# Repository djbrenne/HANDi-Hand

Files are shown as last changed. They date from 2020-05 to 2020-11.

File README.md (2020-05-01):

# HANDi-Hand
Personal, unt-tested, un-released versions of HANDi Hand files. For verified and supported versions, see github.com/blincdev.

**MUX_Assembly.STEP:** The current version of the wrist MUX prototype, including connectors for sensors, servos, and out-of-wrist wires.

**Fit Test.STEP:** An assembly with all the relevant components for testing the fit of the MUX board in the wrist.

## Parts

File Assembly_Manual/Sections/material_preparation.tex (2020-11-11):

% Material Preparation

\chapter{Material Preparation}  % Main chapter title

\label {Material Preparation} 
%---------------------------------------------------------------------------------------------------------------------------------------
%
% MATERIAL PREPARATION
%
%---------------------------------------------------------------------------------------------------------------------------------------

\section{3D Printed Parts}
\textit{Estimated time 17h 0m}

\section{Potentiometers}
\textit{Estimated time 1h 45m}

In the current version, there are nine potentiometers (limited due to the number of analog input pins on the Arduino Mega). The suggested lengths of the connecting wires are found in Table \ref{potentiometer_table}.

\begin{table}[H]
\centering
\caption{Suggested wire lengths for potentiometers}
\label{potentiometer_table}
\begin{tabular}{| l | l |}
\hline
\textbf{Potentiometer ID} & \textbf{Suggested Wire Length}  \\ \hline
D0 & 150 mm \\ \hline
D1P & 150 mm \\ \hline
D1D & 190 mm \\ \hline
D2P & 150 mm \\ \hline
D2I & 190 mm \\ \hline
D3P & 150 mm \\ \hline
D3I & 190 mm \\ \hline
D4P & 150 mm \\ \hline
D5P & 150 mm \\ \hline
\end{tabular}
\end{table} 

Figure \ref{pot_pins} describes the polarity of the potentiometers. To prepare the potentiomters:

\begin{enumerate}
\item Cut off the top lone pin on the potentiometer as short as possible.
\item Solder the wires to the potentiometer and a straight pin header to the other end of each wire. See note below about D0.
\item Use black heat-shrink on the connections near the potentiometer, and coloured heat shrink on the far connections corresponding to the polarity noted in Figure 7.
\item Heat shrink the 3 wires together near the loose end using a light coloured heat shrink tubing. Label the wires here with the potentiometer ID.
\end{enumerate}
\textbf{Note:}  the straight pin headers for the D0 potentiometer must be soldered to the wires \textit{after} the potentiometer is installed in MC – Geared Rotator, and the wires routed through the narrow channel. Black heat-shrink tubing near the potentiometer will not fit in this channel, so it is omitted. 
\begin{figure}[H]
\centering
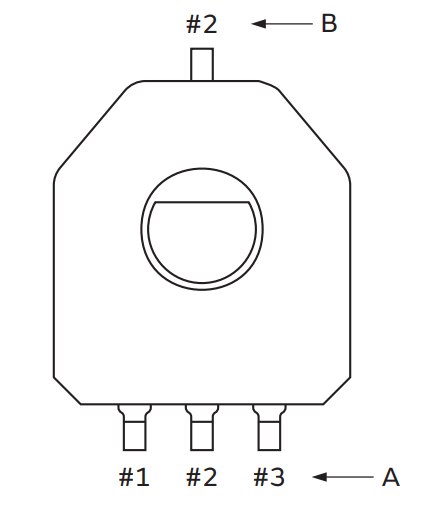
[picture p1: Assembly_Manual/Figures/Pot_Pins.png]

\caption{Potentiometer terminals diagram, viewed from the top (black side facing you). Pin \#1 is GND, pins labelled \#2 are SIG, and pin \#3 is VCC.}
\label{pot_pins}
\end{figure}

\section{FSRs}
\textit{Estimated time 1h 0m}

Each fingertip requires an FSR. The recommended wire length for finger FSRs is 250 mm; for the thumb FSR 200 mm is recommended. 
\begin{enumerate}
\item Solder each wire to the solder tabs of the FSR. 
\item Install FSR in fingertip (see 5.3.1 ).
\item Use black heat-shrink tubing on the connections near the FSR.
\item Solder the wires to straight pin headers.
\item Use yellow and red heat shrink tubing on the connections with the straight pin headers.
\item Heat shrink the two wires together using a light coloured heat shrink, and label the wires here with the ID of the finger they represent.
\end{enumerate}

\section{Screws}

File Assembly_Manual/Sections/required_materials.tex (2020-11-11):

% Required Materials

\chapter{Required Materials}  % Main chapter title

\label {Required Materials} % For referencing the chapter elsewhere, use \ref{Required Materials} 

%----------------------------------------------------------------------------------------

% Define some commands to keep the formatting separated from the content 
\newcommand{\keyword}[1]{\textbf{#1}}
\newcommand{\tabhead}[1]{\textbf{#1}}
\newcommand{\code}[1]{\texttt{#1}}
\newcommand{\file}[1]{\texttt{\bfseries#1}}
\newcommand{\option}[1]{\texttt{\itshape#1}}

%----------------------------------------------------------------------------------------

\section{3D Printed Parts}

The 3D printed parts are designed to be printed in PLA without support material and without rafts, except where indicated. Parts are designed for the print tolerance of a MakerBot Replicator 2. Some filing may be necessary to ensure a smooth running fit between parts.

All files required for 3D printing can be accessed via \href{https://blincdev.ca/}{BLINCdev.ca}. The suggested print specifications for each part are found in Table \ref{3d_printed_parts_list}. The table lists all of the part sets that must be printed for a complete hand. In the event that a particular component is needed, the individual STL files can be found on  \href{https://blincdev.ca/}{BLINCdev.ca} in addition to the grouped parts in Table \ref{3d_printed_parts_list}.

\begin{table}[H]
\centering
\caption{3D Printed Parts Specifications}
\label{3d_printed_parts_list}
\begin{tabular}{|p{4cm}|p{4cm}|p{2cm}|p{2.5cm}|}
\hline
\textbf{Part Name} & \textbf{Print Specifications} & \textbf{Estimated Print Time} & \textbf{Est. Material Weight} \\ \hline
Dorsal Palm & 0.2mm layer, 30\% infill, print with raft & 6h 0m & 64 g \\ \hline
Ventral Palm & 0.2 mm layer, 10\% infill & 1h 55m & 22 g  \\ \hline
Thumb Screw Cap &0.2 mm layer, 10\% infill &0h 15m &2 g  \\ \hline
D2 Full Finger &0.1 mm layer, 50\% infill &3h 36m &11 g  \\ \hline
D3 Full Finger &0.1 mm layer, 50\% infill &3h 36m &11 g  \\ \hline
D4 Full Finger &0.1 mm layer, 50\% infill &3h 36m &11 g  \\ \hline
D5 Full Finger &0.1 mm layer, 50\% infill &3h 36m &11 g  \\ \hline
Full Thumb &0.2 mm layer, 10\% infill &2h 30m &25 g  \\ \hline
Breadboard &0.1 mm layer, 10\% infill &0h 25m &3 g  \\ \hline
Connector Hub &0.2 mm layer, 10\% infill &0h 15m &3 g  \\ \hline
Pot Activator Set of 15 &0.1 mm layer, 10\% infill &0h 10m &1 g  \\ \hline
Pot Placeholder Set of 6 &0.2 mm layer, 10\% infill &0h 10m &2 g  \\ \hline
Servo Spool Full Set &0.1 mm layer, 10\% infill &0h 25m &4 g  \\ \hline
Servo Spur Gear &0.1 mm layer, 10\% infill &0h 5m &1 g  \\ \hline
\textbf{TOTAL:}&\centering{-}  & \textit{\textbf{TODO}} & \textit{\textbf{TODO}} \\ \hline
\end{tabular}
\end{table} 

\section{Off-The-Shelf Parts}
The table below contains all the off-the-shelf parts required for building a complete HANDi Hand. Additional ordering information is provided in Appendix \ref{AppendixA}.
\begin{table}[H]
\centering
\caption{Off-the-Shelf Parts Specifications.\label{ots_parts_table}}
\begin{tabular}{| p{6cm}|  p{7cm} |  p{2cm} |}
\hline
 \textbf{Item} & \textbf{Part Number} & \textbf{QTY}\\ \hline
Rotary position sensor & MuRata SV03A103AEA01R00 & 9 \\ \hline
Force sensitive resistor & Interlink Electronics 34-00004 & 5 \\ \hline
Arduino Mega & Arduino A000067 & 1 \\ \hline
AC / DC 5V 2.5A wall adapter & Qualtek QAWA-18-5-US01 & 2 \\ \hline
DC barrel jack adapter (female) & Sparkfun PRT-10288 &  1 \\ \hline
10 k$\Omega$, 1/8W through-hole resistor & Stackpole Electronics CF18JT10K0 & 5 \\ \hline
12-position header pin (long) & Sullins Connector PREC012SACN-RC & 2 \\ \hline
12-position header pin (short) & Sullins Connector PREC012SAAN-RC & 6 \\ \hline
12-position female socket & Sullins Connector PPTC121LFBN-RC & 2 \\ \hline
3-position female socket & Sullins Connector PPPC031LFBN-RC & 14 \\ \hline
Heat shrink tubing, assorted & Sparkfun PRT-09353 & 1 \\ \hline
Analog RC servo motor & Dymond D47 & 6 \\ \hline
USB Webcam & Microsoft LifeCam HD-3000 & 1 \\ \hline
Textured Neoprene Rubber & McMaster-Carr 8445K61 & 1 \\ \hline
Continuous Flex Wire, 26 AWG & McMaster-Carr 7071K19 & 50 feet \\ \hline
M2 x 25 mm Cheese Head Slotted Machine Screw & McMaster-Carr 91800A023	& 23 \\ \hline
M2 18-8 Washer & McMaster-Carr 93475A195 & 16 \\ \hline
5.9" Zip-Tie & Qualtek 17-M150N-C & 9 \\ \hline
\end{tabular}
\end{table}

\section{Tools}
\begin {multicols}{2}
[
The following tools are required during assembly.]
\begin{itemize}
\item 3D printer
\item M2 screw cutter (or bolt cutters and large flat metal file)
\item Dremel tool with sanding wheel
\item 120 grit sandpaper
\item Small files
\item Narrow flat screwdriver
\item \#0 Philips screwdriver
\item Wire strippers / cutters
\item Soldering iron and solder
\item Heat gun
\item Hobby knife
\item Fine tweezers
\item Needlenose pliers
\end{itemize}
\end{multicols}

\section{Printed Circuit Board}
A custom in-wrist printed circuit board (PCB) has been designed to handle signal and power routing in and out of the hand. The EAGLE files for the PCB are available in the \href{https://github.com/BLINCdev/HANDi-Hand}{HANDi-Hand release repository.} Documentation regarding how to order a PCB from a board manufacturer using these files can also be found in the same location.

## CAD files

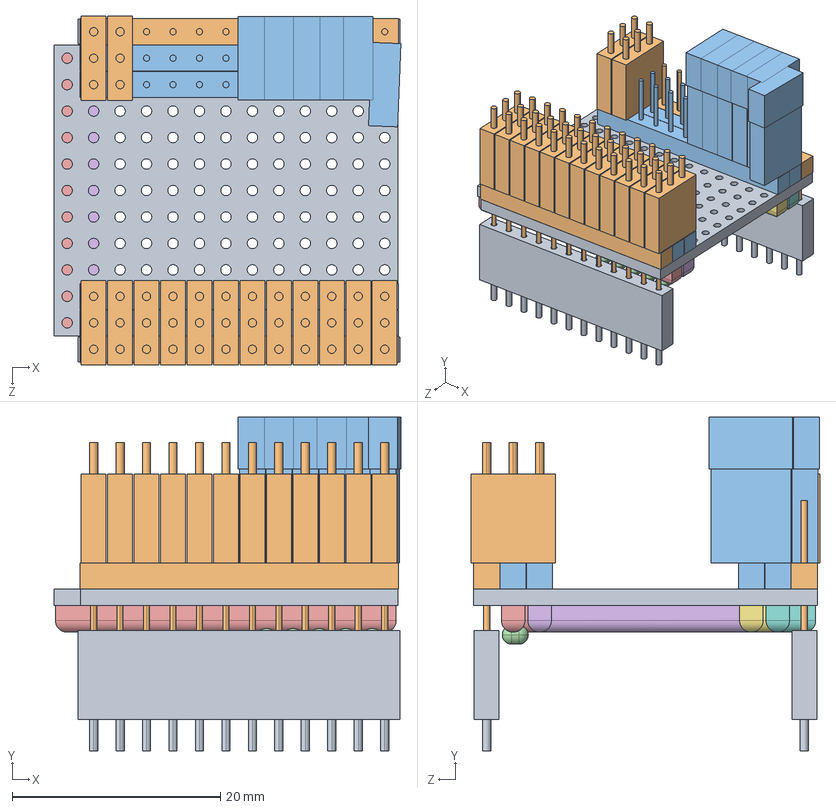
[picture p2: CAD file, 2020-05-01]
MUX_Assembly.STEP
33.3 x 32.0 x 33.5 mm
MUX-Mockup
Long_Conn_Header x 2
Short_Conn_Header x 4
10OHM_FSR x 5
Solder_Lines
Female_Conn_Header_12 x 2
Female_Conn_Header_3 x 14
Female_Conn_Header_Servo x 6

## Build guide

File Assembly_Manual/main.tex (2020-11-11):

%%%%%%%%%%%%%%%%%%%%%%%%%%%%%%%%%%%%%%%%%
% Dylan Brenneis - HANDi-Hand Assembly Manual
% 
% Drafted using the following template, modified for this manual:
%%%%%%%%%%%%%%%%%%%%%%%%%%%%%%%%%%%%%%%%%
% Masters/Doctoral Thesis 
% LaTeX Template
% Version 2.5 (27/8/17)
%
% This template was downloaded from:
% http://www.LaTeXTemplates.com
%
% Version 2.x major modifications by:
% Vel (vel@latextemplates.com)
%
% This template is based on a template by:
% Steve Gunn (http://users.ecs.soton.ac.uk/srg/softwaretools/document/templates/)
% Sunil Patel (http://www.sunilpatel.co.uk/thesis-template/)
%
% Template license:
% CC BY-NC-SA 3.0 (http://creativecommons.org/licenses/by-nc-sa/3.0/)
%
%%%%%%%%%%%%%%%%%%%%%%%%%%%%%%%%%%%%%%%%%

%----------------------------------------------------------------------------------------
%	PACKAGES AND OTHER DOCUMENT CONFIGURATIONS
%----------------------------------------------------------------------------------------

\documentclass[
11pt, % The default document font size, options: 10pt, 11pt, 12pt
oneside, % Two side (alternating margins) for binding by default, uncomment to switch to one side
english, % ngerman for German
% Single line spacing, alternatives: onehalfspacing or doublespacing
%draft, % Uncomment to enable draft mode (no pictures, no links, overfull hboxes indicated)
%nolistspacing, % If the document is onehalfspacing or doublespacing, uncomment this to set spacing in lists to single
%liststotoc, % Uncomment to add the list of figures/tables/etc to the table of contents
%toctotoc, % Uncomment to add the main table of contents to the table of contents
%parskip, % Uncomment to add space between paragraphs
%nohyperref, % Uncomment to not load the hyperref package
headsepline, % Uncomment to get a line under the header
chapterinoneline, % Uncomment to place the chapter title next to the number on one line
%consistentlayout, % Uncomment to change the layout of the declaration, abstract and acknowledgements pages to match the default layout
openany, % Comment out to have chapters, acknowledgements, etc. always start on a right-hand page (creates blank pages where necessary)
]{Manual} % The class file specifying the document structure

\usepackage[utf8]{inputenc} % Required for inputting international characters
\usepackage[T1]{fontenc} % Output font encoding for international characters
\usepackage{lipsum}
\usepackage{mathpazo} % Use the Palatino font by default
\usepackage{amsmath} % Math Package - db
\usepackage{pdfpages} % For picture quote page - db
\usepackage{siunitx}
\usepackage{float}
\usepackage[hidelinks]{hyperref}
\usepackage{caption}
\floatstyle{plaintop}
\restylefloat{table}
\usepackage{longtable}
\usepackage{multicol}
%\usepackage{lscape}
\usepackage{array}
\usepackage{ragged2e}
\newcolumntype{P}[1]{>{\RaggedRight\hspace{0pt}}p{#1}}
\usepackage{pdflscape}
%----------------------------------------------------------------------------------------
%	MARGIN SETTINGS
%----------------------------------------------------------------------------------------

\geometry{
	paper=letterpaper, % Change to letterpaper for US letter
	inner=2.5cm, % Inner margin
	outer=2.5cm, % Outer margin
	%bindingoffset=.5cm, % Binding offset
	top=2.5cm, % Top margin
	bottom=2.5cm, % Bottom margin
	head=21.986pt,
	%showframe, % Uncomment to show how the type block is set on the page
}

%----------------------------------------------------------------------------------------
%	MANUAL INFORMATION
%----------------------------------------------------------------------------------------

\manualtitle{HANDi-Hand Assembly Manual} % Your thesis title, this is used in the title and abstract, print it elsewhere with \ttitle
\author{Dylan J. A. \textsc{Brenneis}} % Your name, this is used in the title page and abstract, print it elsewhere with \authorname

\AtBeginDocument{
\hypersetup{pdftitle=\ttitle} % Set the PDF's title to your title
\hypersetup{pdfauthor=\authorname} % Set the PDF's author to your name
}

\begin{document}

\frontmatter % Use roman page numbering style (i, ii, iii, iv...) for the pre-content pages

\pagestyle{plain} % Default to the plain heading style until the thesis style is called for the body content

%----------------------------------------------------------------------------------------
%	TITLE PAGE
%----------------------------------------------------------------------------------------

\begin{titlepage}

\begin{figure}
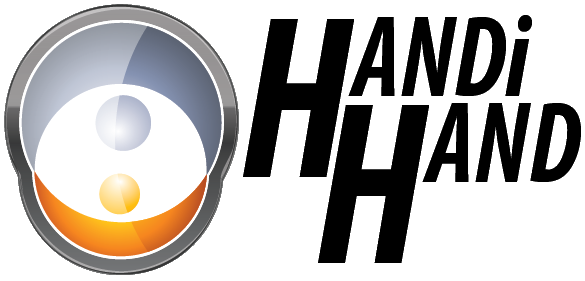
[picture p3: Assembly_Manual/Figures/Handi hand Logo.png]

\end{figure}

\begin{flushright}
\null
\vfill
{\Huge \bfseries \ttitle\par}\vspace{0.6cm} % Manual title
\Large{\textit{Version 2.0}}

\href{http://www.dylanbrenneis.ca}{Dylan J. A. Brenneis}\\%\authorname} % Author name - remove the \href bracket to remove the link
August 2020
\end{flushright}
\end{titlepage}

%----------------------------------------------------------------------------------------
%	INTRODUCTION PAGE
%----------------------------------------------------------------------------------------

\begin{abstract}
\setcounter{page}{2}
\addchaptertocentry{Introduction} % Add the abstract to the table of contents
The HANDi Hand is an open-source robotic platform specifically designed for machine learning research in prosthetic control. The inexpensive and easily modifiable hardware allows versatility for research studies, and the suite of sensors provides valuable information for machine learning and prosthetics research. 

This assembly manual outlines all the information required to print and source parts, and assemble the HANDi Hand as currently designed. The hand takes an estimated 30 hours to build.

The open-source release provides all solid-modelling files, .stl files, Arduino code, and assembly instruction required to construct a fully functional HANDi Hand, and should also give the maker enough flexibility to make alterations to the design as necessary to suit their own needs. Both left and right hand versions are available. To contact the original designers, or to receive support for your build, please visit  \href{https://blincdev.ca/}{BLINCdev.ca}.
\section*{Version 2.0 Updates}
The HANDi Hand was originally released in August 2017.\footnote{D. J. A. Brenneis, M. R. Dawson, P. M. Pilarski, “\href{https://sites.ualberta.ca/~pilarski/docs/papers/Brenneis_2017_MEC_preprint.pdf}{Development of the HANDi Hand: An Inexpensive, Multi-Articulating, Sensorized Hand for Machine Learning Research in Myoelectric Control},” Proc. of MEC’17: Myoelectric Controls Symposium, Fredericton, New Brunswick, August 15-18, 2017.} This updated assembly manual includes a number of changes that lower the overall cost and increase the ease of building the hand, as well as compensating for the discontinuation of the previous servo-motors. The hand's performance characteristics remain similar to that published in MEC '17. The main changes include:
\begin{itemize}
\item Redesign for Dymond D47 servos
\item Design of in-wrist PCB
\item Redesign for smaller, more inexpensive camera
\item Update specifications for UV-resistant zip-tie cables
\item More comprehensive build documentation, including assembly videos
\end{itemize}
\end{abstract}
%----------------------------------------------------------------------------------------
%	LIST OF CONTENTS/FIGURES/TABLES PAGES
%----------------------------------------------------------------------------------------

\tableofcontents % Prints the main table of contents

\listoftables % Prints the list of tables

\listoffigures % Prints the list of figures

%----------------------------------------------------------------------------------------
%	DEFINITIONS
%----------------------------------------------------------------------------------------
\newpage
\addchaptertocentry{Glossary of Terms}
\noindent\textbf{\Huge{Glossary of Terms}}
\vspace{1cm}

\noindent\textbf{Digits}: The digits are referred to by standard numbering, beginning with the thumb as D1 as shown in Figure~\ref{fig:finger_nums}.
\begin{figure}[H]
\centering
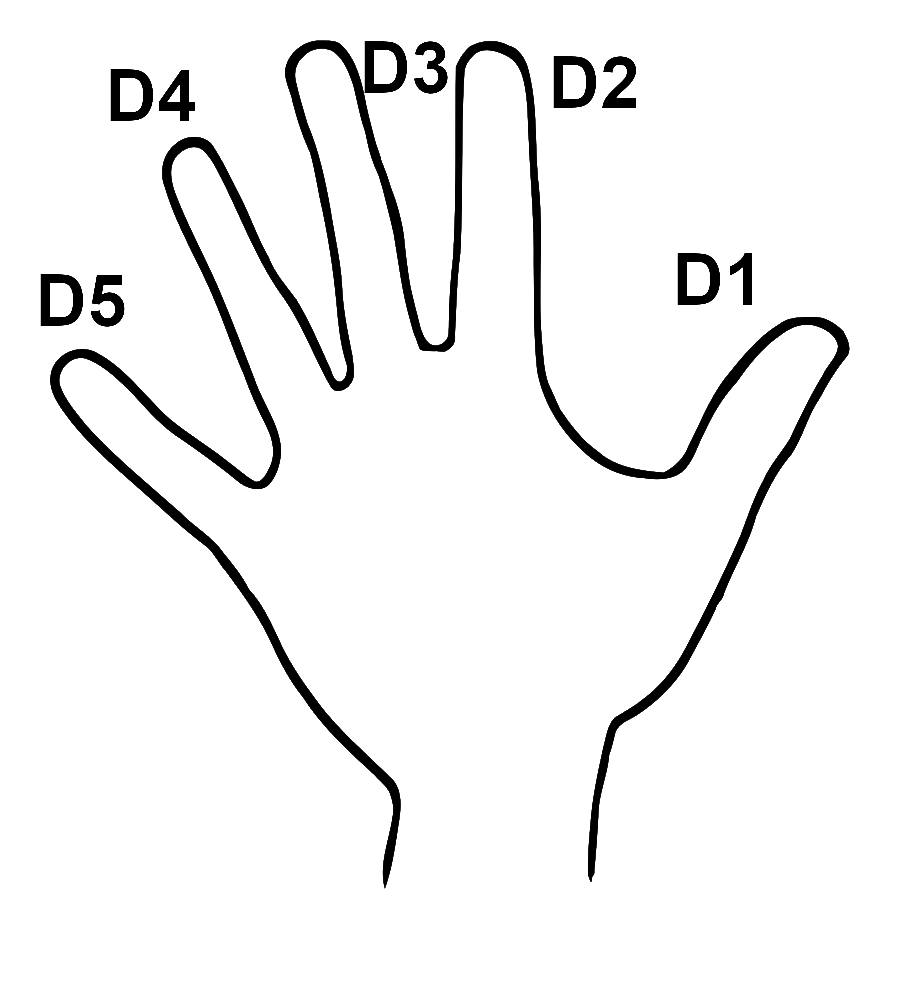
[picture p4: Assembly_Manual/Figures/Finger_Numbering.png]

\caption{Numbering scheme used for finger naming.}
\label{fig:finger_nums}
\end{figure}
\noindent\textbf{Joints}: The joints are named in accordance with Figure~\ref{fig:joint_nums}. The names are constructed first with a digit indicator (i.e. D2) followed by a joint indicator D, I or P, indicating distal, intermediate, or proximal respectively. Potentiometers are named for the joints that they measure. The digit D0 refers to thumb rotation.
\begin{figure}[H]
\centering
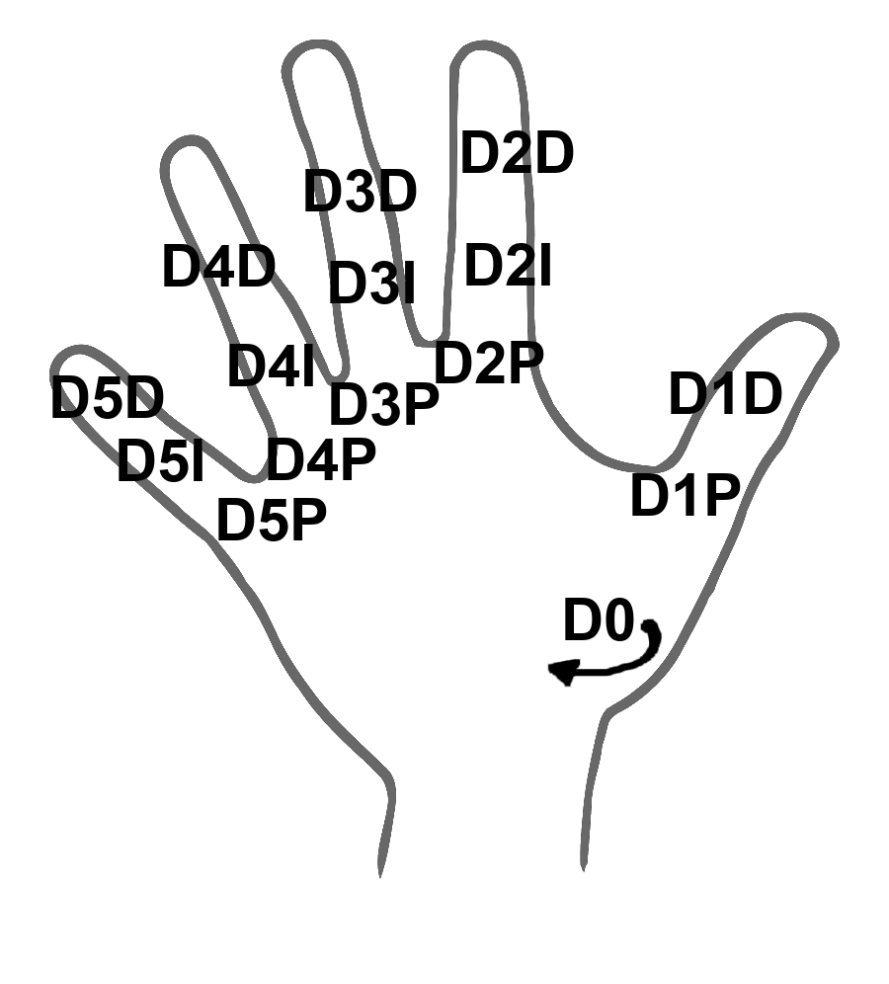
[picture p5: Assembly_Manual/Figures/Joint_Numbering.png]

\caption{Numbering scheme used for joint naming.}
\label{fig:joint_nums}
\end{figure}

\noindent\textbf{Finger Parts}: Each phalanx of the finger is made up of multiple parts. The part names are contrived according to the following convention:
\begin{enumerate}
\item Phalanx indicator. PP = Proximal Phalanx, IP = Intermediate Phalanx, DP = Distal Phalanx, MC = Metacarpal
\item Part position indicator. P = Proximal, D = Distal
\item Position modifier. There are sometimes multiple parts in the same location that must be differentiated by their function (pivot, main, lock, tip, etc).
\item Handedness indicator. R = Right Hand, L = Left Hand
\end{enumerate}
An example part name would be \textbf{IP-P Pivot R}, for the proximal portion of the intermediate phalanx corresponding to the pivot, for the right-hand version of the HANDi Hand.
\newpage

%----------------------------------------------------------------------------------------
%	MAIN CONTENT 
%----------------------------------------------------------------------------------------

\mainmatter % Begin numeric (1,2,3...) page numbering

\pagestyle{thesis} % Return the page headers back to the "thesis" style

% Include the steps of assembly as separate files from the Steps folder
% Uncomment the lines as you write the chapters

\include{Sections/required_materials}
\include{Sections/flowchart}
\include{Sections/material_preparation}
\include{Sections/thumb_assembly}
\include{Sections/finger_assembly}
\include{Sections/servo_installation}
\include{Sections/signal_board}
\include{Sections/ventral_palm}
\include{Sections/palm_grips}
\include{Sections/wiring}

%----------------------------------------------------------------------------------------
%	MANUAL CONTENT - APPENDICES
%----------------------------------------------------------------------------------------

\appendix % Cue to tell LaTeX that the following "chapters" are Appendices
% Include the appendices of the thesis as separate files from the Appendices folder
% Uncomment the lines as you write the Appendices

\include{Sections/appendix_a}
\include{Sections/appendix_b}
%\include{Appendices/AppendixC}

\end{document}

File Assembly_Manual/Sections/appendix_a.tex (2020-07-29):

% Appendix A

\chapter{Commercial Off-The-Shelf Parts Information} % Main appendix title

\label{AppendixA}

This appendix contains detailed ordering information for the off-the-shelf parts used in the HANDi Hand. Links to specific vendors are supplied for convenience only; no affiliation between BLINCdev and the vendors exists or is implied. Cost information is provided to give the builder an estimate of the cost of the project, and is accurate as of August 2020.
\newpage
%\begin{landscape}
\begin{longtable}{| P{3cm} | P{4cm} | P{2cm} | P{1cm} | P{1.5cm} | P{1.5cm} | P{1cm} |}
\caption{Detailed information for off-the-shelf parts used in the HANDi Hand. Click on part numbers for specific links.}
\label{detailed_cots}

\\ \hline \textbf{Item}  & \textbf{Part Number} & \textbf{Vendor} & \textbf{QTY} & \textbf{Cost / Item} & \textbf{Ext. Cost} & \textbf{Curr.} \\ \hline
\endfirsthead

\hline \textbf{Item}  & \textbf{Part Number} & \textbf{Vendor} & \textbf{QTY} & \textbf{Cost / Item} & \textbf{Ext. Cost} & \textbf{Curr.} \\ \hline
\endhead

\hline \multicolumn{7}{|r|}{\textit{Continued on next page...}} \\ \hline \endfoot

\hline \multicolumn{7}{|r|}{\textit{End of table.}} \\ \hline \endlastfoot

Rotary position sensor 						& \href{https://www.digikey.ca/en/products/detail/murata-electronics/SV03A103AEA01R00/4359898}{MuRata SV03A103AEA01R00} 														& DigiKey 			& 9 		& \$2.33 	& \$20.97		& CAD \\ \hline
Force sensitive resistor 						& \href{https://www.digikey.ca/en/products/detail/interlink-electronics/34-00004/2798665}{Interlink Electronics 34-00004}																& DigiKey 			& 5  		& \$16.20 	& \$71.08		& CAD \\ \hline
Arduino Mega 								& \href{https://www.digikey.ca/en/products/detail/arduino/A000067/2639006?s=N4IgTCBcDaIIwAYCsCC0i4A5UDkAiIAugL5A}{Arduino A000067} 												& DigiKey 			& 1 		& \$56.86 	& \$56.86		& CAD  \\ \hline
AC / DC 5V 2.5A wall adapter 					& \href{https://www.digikey.ca/en/products/detail/qualtek/QAWA-18-5-US01/6412294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}{Qualtek QAWA-18-5-US01}							& DigiKey 			& 2 		& \$25.33 	& \$50.66		& CAD \\ \hline
DC barrel jack adapter (female) 				& \href{https://www.digikey.ca/en/products/detail/sparkfun-electronics/PRT-10288/6163697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}{Sparkfun PRT-10288} 									& DigiKey	 		& 1 		& \$4.36 	& \$4.36		& CAD  \\ \hline
10 k$\Omega$, 1/8W through-hole resistor 		& \href{https://www.digikey.ca/en/products/detail/stackpole-electronics-inc/CF18JT10K0/1741566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}{Stackpole Electronics CF18JT10K0} 				& DigiKey 			& 5  		& \$0.16 	& \$0.80		& CAD \\ \hline
12-position header pin (long) 					& \href{https://www.digikey.ca/en/products/detail/sullins-connector-solutions/PREC012SACN-RC/2775974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}{Sullins Connector PREC012SACN-RC} 	& DigiKey 			& 2  		& \$0.49 	& \$0.98		& CAD \\ \hline
12-position header pin (short) 					& \href{https://www.digikey.ca/en/products/detail/sullins-connector-solutions/PREC012SAAN-RC/2774842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}{Sullins Connector PREC012SAAN-RC} 	& DigiKey 			& 6  		& \$0.38 	& \$2.28		& CAD \\ \hline
12-position female socket 						& \href{https://www.digikey.ca/en/products/detail/sullins-connector-solutions/PPTC121LFBN-RC/807231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}{Sullins Connector PPTC121LFBN-RC} 		& DigiKey 			& 2  		& \$1.15 	& \$2.30		& CAD \\ \hline
3-position female socket 						& \href{https://www.digikey.ca/en/products/detail/sullins-connector-solutions/PPPC031LFBN-RC/810175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}{Sullins Connector PPPC031LFBN-RC} 		& DigiKey 			& 14  	& \$0.55 	& \$7.25		& CAD \\ \hline
Heat shrink tubing, assorted 					& \href{https://www.digikey.ca/en/products/detail/qualtek/Q2-F-RK4-1-16-11-6IN-39/1210262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}{Qualtek Q2-F-RK4-1/16-11-6IN-39} 					& DigiKey	 		& 1 		& \$2.96 	& \$2.96		& CAD  \\ \hline
7.87" Black Zip-Tie 							& \href{https://www.digikey.ca/en/products/detail/advanced-cable-ties-inc/AL-08-18-0-C/10378818}{Advanced Cable Ties AL-08-18-0-C}														& DigiKey 			& Pack of 100\footnote{Only 5 zip-ties required for assembly.} 	& \$6.09 	& \$6.09		& CAD \\ \hline
Analog RC servo motor 						& \href{https://www.dymondusa.com/Servo-11305-D47-Power-Servo.html}{Dymond 11305 D47} 																					& Dymond 		& 6  		& \$21.95 	& \$131.70	& USD \\ \hline
USB Webcam 								& \href{https://www.amazon.ca/Microsoft-Lifecam-HD-3000-Webcam-Black/dp/B009VL9YJ2}{Microsoft LifeCam HD-3000} 																& Amazon 		& 1 		& \$38.59 	& \$38.59		& CAD  \\ \hline
1/32" Textured Neoprene Rubber, 40A Durometer 	& \href{https://www.mcmaster.com/8445K61-8445K161/}{McMaster-Carr 8445K61} 																							& McMaster-Carr 	& 12" x 12"		& \$12.45 & \$12.45		& USD \\ \hline
Continuous Flex Wire, 26 AWG 					& \href{https://www.mcmaster.com/7071K19/}{McMaster-Carr 7071K19} 																									& McMaster-Carr 	& 50 feet 			& \$1.20 	& \$60.00 		& USD  \\ \hline
M2 x 25 mm Cheese Head Slotted Machine Screw 	& \href{https://www.mcmaster.com/91800A023/}{McMaster-Carr 91800A023}																									& McMaster-Carr 	& Pack of 50*\footnote{Only 23 screws needed for assembly.}		& \$8.41 	& \$8.41		& USD  \\ \hline
M2 18-8 Washer 							& \href{https://www.mcmaster.com/93475A195/}{McMaster-Carr 93475A195}																									& McMaster-Carr	& Pack of 100\footnote{Only 16 washers needed for assembly.}  	& \$1.06 	& \$1.06		& USD \\ \hline
\textbf{APPROXIMATE TOTAL:} & & & & & \$550\footnote{This is a rough estimate, assuming \$1.35 CAD = \$1.00 USD. Delivery fees and taxes are not included.} & CAD \\ \hline
\end{longtable}
%\end{landscape}

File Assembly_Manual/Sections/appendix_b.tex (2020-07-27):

% Appendix B

\chapter{Grip Pattern Template} % Main appendix title

\label{AppendixB}

The following page contains a template you can use to cut out the neoprene rubber grips. When printing this page, be sure to check in your print settings that you are using the original scale of the document.

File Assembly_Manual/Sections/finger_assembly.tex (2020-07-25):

% Finger Assembly

\chapter{Finger Assembly}  % Main chapter title

\label{Finger Assembly} 
%---------------------------------------------------------------------------------------------------------------------------------------
%
% FINGER ASSEMBLY
%
%---------------------------------------------------------------------------------------------------------------------------------------

\textit{Estimated time 0h 15m per finger}

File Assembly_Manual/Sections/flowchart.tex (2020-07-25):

% Assembly Flowchart

\chapter{Assembly Flowchart}  % Main chapter title

\label {Assembly Flowchart} 
%---------------------------------------------------------------------------------------------------------------------------------------
%
% ASSEMBLY FLOWCHART
%
%---------------------------------------------------------------------------------------------------------------------------------------
A particular order of operations must be followed when assembling the hand, and is outlined in the following flowchart. A process described in any bubble cannot be completed until all items attached to incoming arrows have been completed.
\begin{figure}
\centering
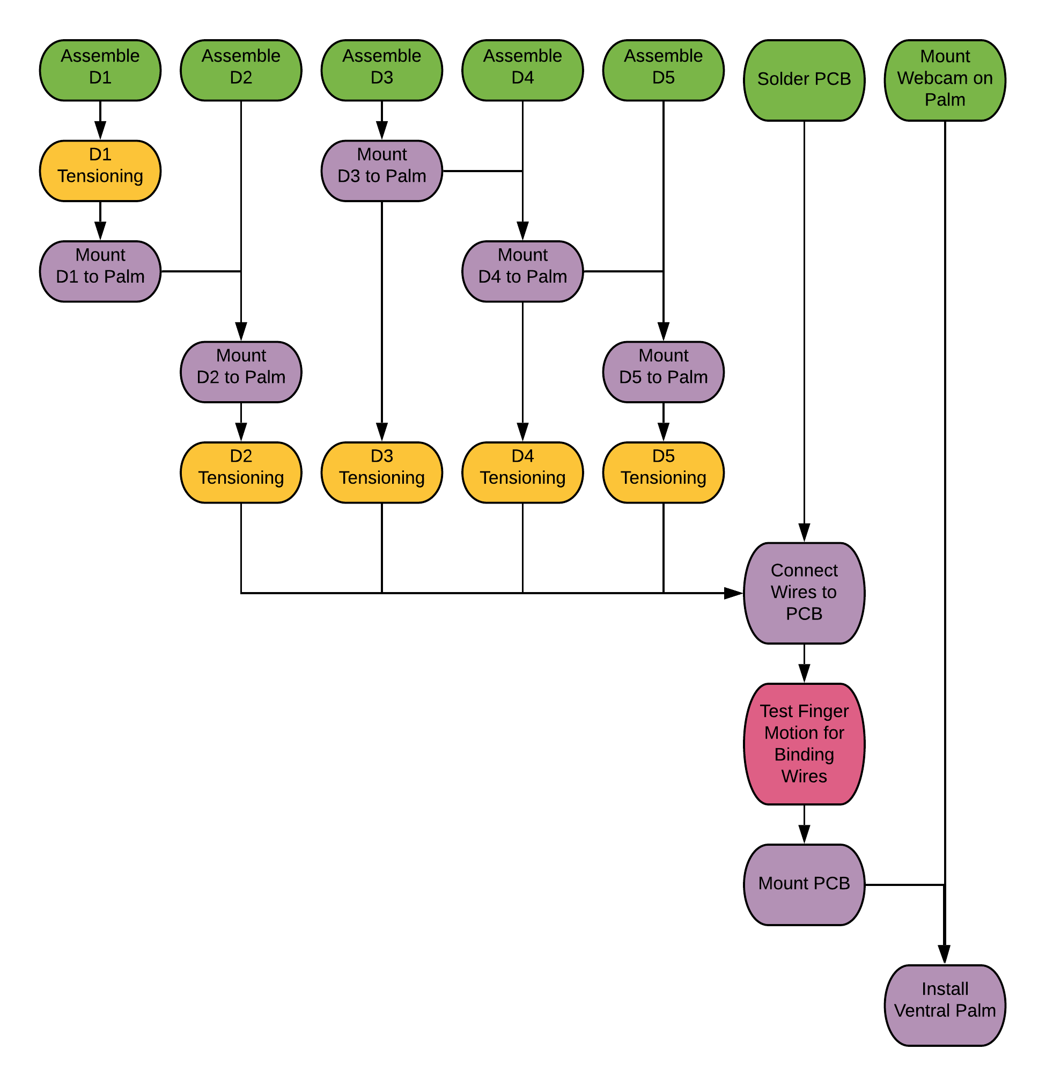
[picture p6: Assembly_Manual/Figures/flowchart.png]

\caption{Flowchart depicting the order of operations in assembling the HANDi Hand.}
\label{fig:flowchart}
\end{figure}

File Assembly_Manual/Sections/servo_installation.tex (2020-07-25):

% Servo Installation and Finger Tensioning

\chapter{Servo Installation and Finger Tensioning}  % Main chapter title

\label{Servo Installation and Finger Tensioning} 
%---------------------------------------------------------------------------------------------------------------------------------------
%
% Servo Installation and Finger Tensioning
%
%---------------------------------------------------------------------------------------------------------------------------------------

\textit{Estimated time 0h 7m per finger}

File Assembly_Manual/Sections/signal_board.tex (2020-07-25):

% Signal Routing Board

\chapter{Signal Routing Board}  % Main chapter title

\label{Signal Routing Board} 
%---------------------------------------------------------------------------------------------------------------------------------------
%
% SIGNAL ROUTING BOARD
%
%---------------------------------------------------------------------------------------------------------------------------------------

\textit{Estimated time 0h XXm}

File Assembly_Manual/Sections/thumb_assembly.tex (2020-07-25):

% Thumb Assembly

\chapter{Thumb Assembly}  % Main chapter title

\label {Thumb Assembly} 
%---------------------------------------------------------------------------------------------------------------------------------------
%
% THUMB ASSEMBLY
%
%---------------------------------------------------------------------------------------------------------------------------------------

\textit{Estimated time 1h 0m}

\section{Part Assembly}

\section{Mounting to Palm}

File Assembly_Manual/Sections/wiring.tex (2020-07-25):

% Wiring

\chapter{Wiring}  % Main chapter title

\label{Wiring} 
%---------------------------------------------------------------------------------------------------------------------------------------
%
% WIRING	
%
%---------------------------------------------------------------------------------------------------------------------------------------

\textit{Estimated time 1h 0m}

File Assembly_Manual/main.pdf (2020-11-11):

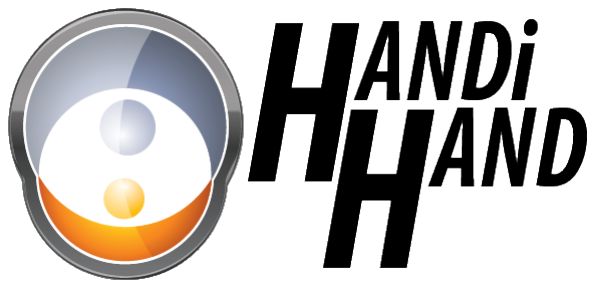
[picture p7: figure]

# HANDi-Hand Assembly Manual

### Version 2.0

## Dylan J. A. Brenneis (http://www.dylanbrenneis.ca) August 2020

ii

# Introduction

The HANDi Hand is an open-source robotic platform specifically designed for machine learning research in prosthetic control. The inexpensive and easily modifiable hardware allows versatility for research studies, and the suite of sensors provides valuable information for machine learning and prosthetics research.
This assembly manual outlines all the information required to print and source parts, and assemble the HANDi Hand as currently designed. The hand takes an estimated 30 hours to build. The open-source release provides all solid-modelling files, .stl files, Arduino code, and assembly instruction required to construct a fully functional HANDi Hand, and should also give the maker enough flexibility to make alterations to the design as necessary to suit their own needs. Both left and right hand versions are available. To contact the original designers, or to receive support for your build, please visit BLINCdev.ca.

### Version 2.0 Updates

The HANDi Hand was originally released in August 2017.¹ This updated assembly manual includes a number of changes that lower the overall cost and increase the ease of building the hand, as well as compensating for the discontinuation of the previous servo-motors. The hand’s performance characteristics remain similar to that published in MEC ’17. The main changes include:

- Redesign for Dymond D47 servos
- Design of in-wrist PCB
- Redesign for smaller, more inexpensive camera
- Update specifications for UV-resistant zip-tie cables
- More comprehensive build documentation, including assembly videos

1D. J. A. Brenneis, M. R. Dawson, P. M. Pilarski, “Development of the HANDi Hand: An Inexpensive, Multi-Articulating, Sensorized Hand for Machine Learning Research in Myoelectric Control,” (https://sites.ualberta.ca/~pilarski/docs/papers/Brenneis_2017_MEC_preprint.pdf) Proc. of MEC’17: Myoelectric Controls Symposium, Fredericton, New Brunswick, August 15-18, 2017.

iii

# Contents

Introduction | ii
Glossary of Terms | vi
1 Required Materials | 1
2 Assembly Flowchart | 4
3 Material Preparation | 6
4 Thumb Assembly | 8
5 Finger Assembly | 9
6 Servo Installation and Finger Tensioning | 10
7 Signal Routing Board | 11
8 Ventral Palm Cover and USB Webcam | 12
9 Palm Grips | 13
10 Wiring | 14
A Commercial Off-The-Shelf Parts Information | 15
B Grip Pattern Template | 18

iv

# List of Tables

1.1 3D Printed Parts Specifications | | 1
1.2 Off-the-Shelf Parts Specifications | | 2
3.1 Suggested wire lengths for potentiometers | | 6

A.1 Detailed information for off-the-shelf parts used in the HANDi Hand. Click on part
numbers for specific links | 16

v

# List of Figures

1 | Numbering scheme used for finger naming | | vi
2 | Numbering scheme used for joint naming | | vi
2.1 Flowchart depicting the order of operations in assembling the HANDi Hand | | 5

3.1 Potentiometer terminals diagram, viewed from the top (black side facing you). Pin
| #1 is GND, pins labelled #2 are SIG, and pin #3 is VCC | | 7

vi

# Glossary of Terms

Digits: The digits are referred to by standard numbering, beginning with the thumb as D1 as shown in Figure 1.

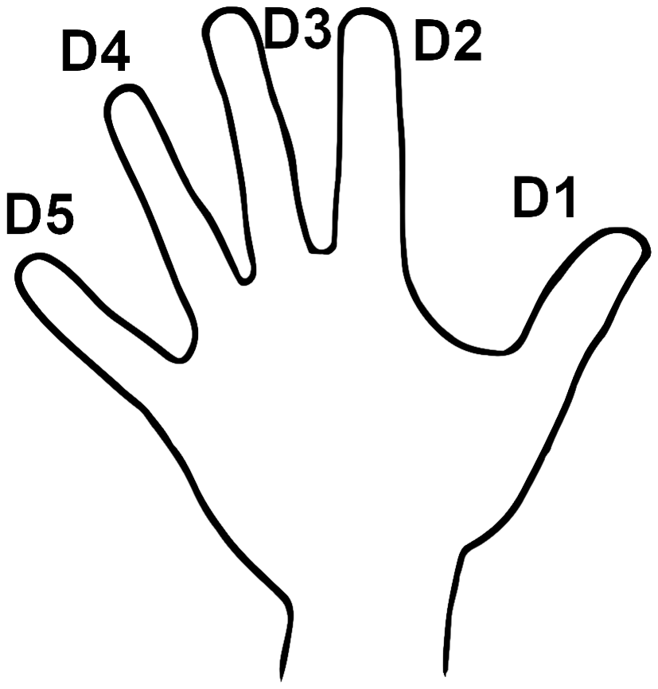
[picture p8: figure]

FIGURE 1: Numbering scheme used for finger naming.

Joints: The joints are named in accordance with Figure 2. The names are constructed first with a digit indicator (i.e. D2) followed by a joint indicator D, I or P, indicating distal, intermediate, or proximal respectively. Potentiometers are named for the joints that they measure. The digit D0 refers to thumb rotation.

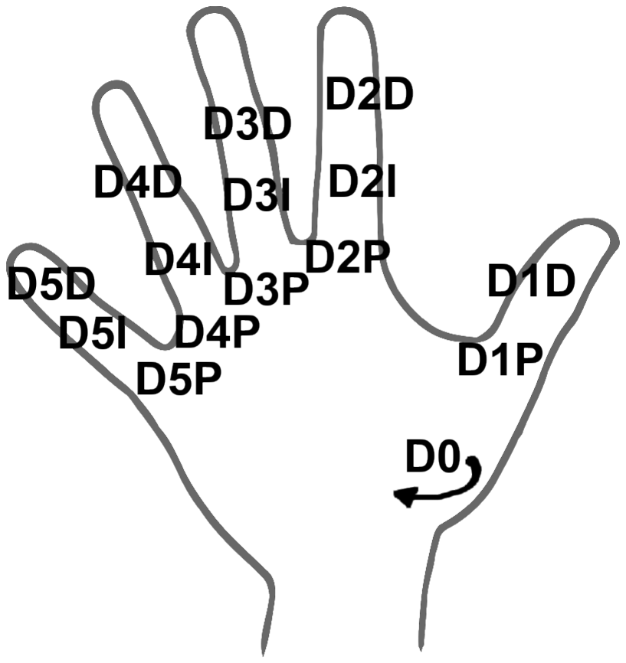
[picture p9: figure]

FIGURE 2: Numbering scheme used for joint naming.

Finger Parts: Each phalanx of the finger is made up of multiple parts. The part names are contrived according to the following convention:

vii

1. Phalanx indicator. PP = Proximal Phalanx, IP = Intermediate Phalanx, DP = Distal Phalanx, MC = Metacarpal
2. Part position indicator. P = Proximal, D = Distal
3. Position modifier. There are sometimes multiple parts in the same location that must be differentiated by their function (pivot, main, lock, tip, etc).
4. Handedness indicator. R = Right Hand, L = Left Hand

An example part name would be IP-P Pivot R, for the proximal portion of the intermediate phalanx corresponding to the pivot, for the right-hand version of the HANDi Hand.

1

# 1 Required Materials

### 1.1 3D Printed Parts

The 3D printed parts are designed to be printed in PLA without support material and without rafts, except where indicated. Parts are designed for the print tolerance of a MakerBot Replicator
2. Some filing may be necessary to ensure a smooth running fit between parts.
All files required for 3D printing can be accessed via BLINCdev.ca. The suggested print specifications for each part are found in Table 1.1. The table lists all of the part sets that must be printed for a complete hand. In the event that a particular component is needed, the individual STL files can be found on BLINCdev.ca in addition to the grouped parts in Table 1.1.

TABLE 1.1: 3D Printed Parts Specifications

Part Name | Print Specifications | Estimated Print Time | Est. Material Weight
Dorsal Palm | 0.2mm layer, 30% infill, print with raft | 6h 0m | 64 g
Ventral Palm | 0.2 mm layer, 10% infill | 1h 55m | 22 g
Thumb Screw Cap | 0.2 mm layer, 10% infill | 0h 15m | 2 g
D2 Full Finger | 0.1 mm layer, 50% infill | 3h 36m | 11 g
D3 Full Finger | 0.1 mm layer, 50% infill | 3h 36m | 11 g
D4 Full Finger | 0.1 mm layer, 50% infill | 3h 36m | 11 g
D5 Full Finger | 0.1 mm layer, 50% infill | 3h 36m | 11 g
Full Thumb | 0.2 mm layer, 10% infill | 2h 30m | 25 g
Breadboard | 0.1 mm layer, 10% infill | 0h 25m | 3 g
Connector Hub | 0.2 mm layer, 10% infill | 0h 15m | 3 g
Pot Activator Set of 15 | 0.1 mm layer, 10% infill | 0h 10m | 1 g
Pot Placeholder Set of 6 | 0.2 mm layer, 10% infill | 0h 10m | 2 g
Servo Spool Full Set | 0.1 mm layer, 10% infill | 0h 25m | 4 g
Servo Spur Gear | 0.1 mm layer, 10% infill | 0h 5m | 1 g
TOTAL: | - | TODO | TODO

Chapter 1. Required Materials | 2

### 1.2 Off-The-Shelf Parts

The table below contains all the off-the-shelf parts required for building a complete HANDi Hand. Additional ordering information is provided in Appendix A.

TABLE 1.2: Off-the-Shelf Parts Specifications.

Item | Part Number | QTY
Rotary position sensor | MuRata SV03A103AEA01R00 | 9
Force sensitive resistor | Interlink Electronics 34-00004 | 5
Arduino Mega | Arduino A000067 | 1
AC / DC 5V 2.5A wall adapter | Qualtek QAWA-18-5-US01 | 2
DC barrel jack adapter (female) | Sparkfun PRT-10288 | 1
10 kΩ, 1/8W through-hole resistor | Stackpole Electronics CF18JT10K0 | 5
12-position header pin (long) | Sullins Connector PREC012SACN-RC | 2
12-position header pin (short) | Sullins Connector PREC012SAAN-RC | 6
12-position female socket | Sullins Connector PPTC121LFBN-RC | 2
3-position female socket | Sullins Connector PPPC031LFBN-RC | 14
Heat shrink tubing, assorted | Sparkfun PRT-09353 | 1
Analog RC servo motor | Dymond D47 | 6
USB Webcam | Microsoft LifeCam HD-3000 | 1
Textured Neoprene Rubber | McMaster-Carr 8445K61 | 1
Continuous Flex Wire, 26 AWG | McMaster-Carr 7071K19 | 50 feet
M2 x 25 mm Cheese Head Slotted Machine Screw | McMaster-Carr 91800A023 | 23
M2 18-8 Washer | McMaster-Carr 93475A195 | 16
5.9" Zip-Tie | Qualtek 17-M150N-C | 9

### 1.3 Tools

The following tools are required during assembly.

- 3D printer
- M2 screw cutter (or bolt cutters and large flat metal file)
- Dremel tool with sanding wheel
- 120 grit sandpaper
- Small files
- Narrow flat screwdriver
- #0 Philips screwdriver
- Wire strippers / cutters
- Soldering iron and solder
- Heat gun
- Hobby knife
- Fine tweezers
- Needlenose pliers

Chapter 1. Required Materials | 3

### 1.4 Printed Circuit Board

A custom in-wrist printed circuit board (PCB) has been designed to handle signal and power routing in and out of the hand. The EAGLE files for the PCB are available in the HANDi-Hand release repository. (https://github.com/BLINCdev/HANDi-Hand) Documentation regarding how to order a PCB from a board manufacturer using these files can also be found in the same location.

4

# 2 Assembly Flowchart

A particular order of operations must be followed when assembling the hand, and is outlined in the following flowchart. A process described in any bubble cannot be completed until all items attached to incoming arrows have been completed.

Chapter 2. Assembly Flowchart | 5

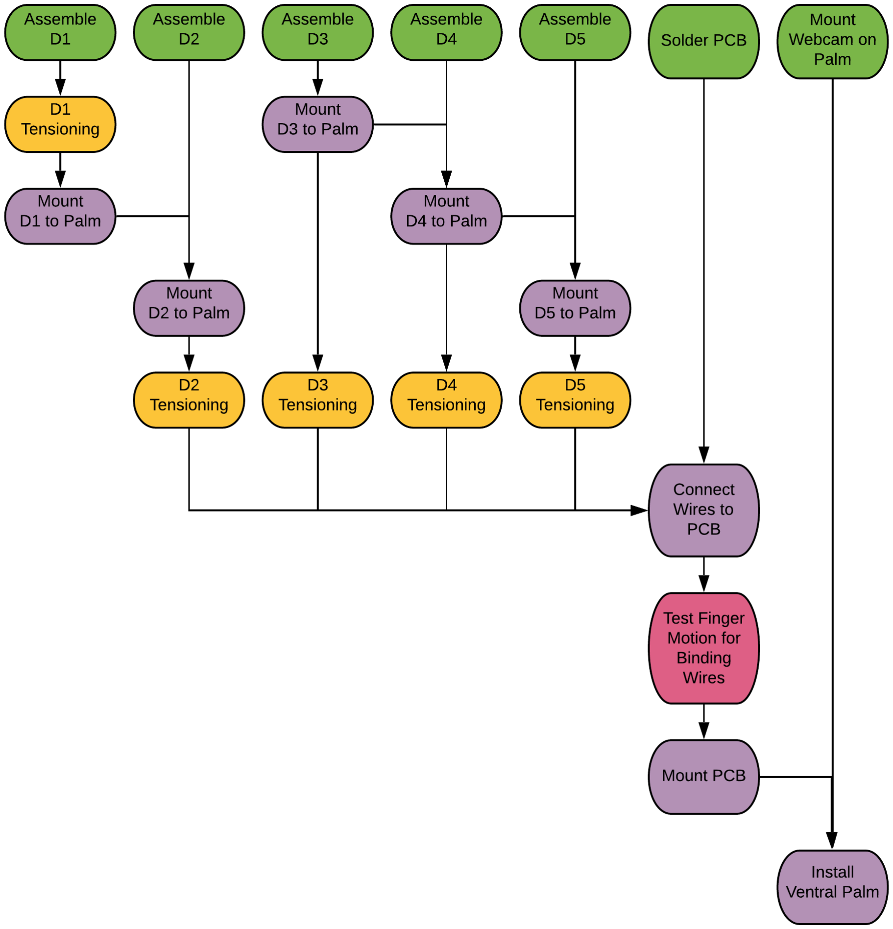
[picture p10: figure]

FIGURE 2.1: Flowchart depicting the order of operations in assembling the HANDi Hand.

6

# 3 Material Preparation

### 3.1 3D Printed Parts

Estimated time 17h 0m

### 3.2 Potentiometers

Estimated time 1h 45m
In the current version, there are nine potentiometers (limited due to the number of analog input pins on the Arduino Mega). The suggested lengths of the connecting wires are found in Table 3.1.

TABLE 3.1: Suggested wire lengths for potentiometers

Potentiometer ID | Suggested Wire Length
D0 | 150 mm
D1P | 150 mm
D1D | 190 mm
D2P | 150 mm
D2I | 190 mm
D3P | 150 mm
D3I | 190 mm
D4P | 150 mm
D5P | 150 mm

Figure 3.1 describes the polarity of the potentiometers. To prepare the potentiomters:

1. Cut off the top lone pin on the potentiometer as short as possible.
2. Solder the wires to the potentiometer and a straight pin header to the other end of each wire. See note below about D0.
3. Use black heat-shrink on the connections near the potentiometer, and coloured heat shrink on the far connections corresponding to the polarity noted in Figure 7.
4. Heat shrink the 3 wires together near the loose end using a light coloured heat shrink tubing. Label the wires here with the potentiometer ID.

Chapter 3. Material Preparation | 7

Note: the straight pin headers for the D0 potentiometer must be soldered to the wires after the potentiometer is installed in MC – Geared Rotator, and the wires routed through the narrow channel. Black heat-shrink tubing near the potentiometer will not fit in this channel, so it is omitted.


FIGURE 3.1: Potentiometer terminals diagram, viewed from the top (black side facing you). Pin #1 is GND, pins labelled #2 are SIG, and pin #3 is VCC.

### 3.3 FSRs

Estimated time 1h 0m
Each fingertip requires an FSR. The recommended wire length for finger FSRs is 250 mm; for the thumb FSR 200 mm is recommended.
1. Solder each wire to the solder tabs of the FSR.
2. Install FSR in fingertip (see 5.3.1 ).
3. Use black heat-shrink tubing on the connections near the FSR.
4. Solder the wires to straight pin headers.
5. Use yellow and red heat shrink tubing on the connections with the straight pin headers.
6. Heat shrink the two wires together using a light coloured heat shrink, and label the wires here with the ID of the finger they represent.

### 3.4 Screws

8

# 4 Thumb Assembly

Estimated time 1h 0m

### 4.1 Part Assembly

### 4.2 Mounting to Palm

9

# 5 Finger Assembly

Estimated time 0h 15m per finger

10

# 6 Servo Installation and Finger Tensioning

Estimated time 0h 7m per finger

11

# 7 Signal Routing Board

Estimated time 0h XXm

12

# 8 Ventral Palm Cover and USB Webcam

Estimated time 0h 20m

13

# 9 Palm Grips

Estimated time 1h 15m

14

# 10 Wiring

Estimated time 1h 0m

15

# A Commercial Off-The-Shelf Parts Information

This appendix contains detailed ordering information for the off-the-shelf parts used in the HANDi Hand. Links to specific vendors are supplied for convenience only; no affiliation between BLINCdev and the vendors exists or is implied. Cost information is provided to give the builder an estimate of the cost of the project, and is accurate as of August 2020.

Appendix A. Commercial Off-The-Shelf Parts Information | 16

TABLE A.1: Detailed information for off-the-shelf parts used in the HANDi Hand. Click on part numbers for specific links.

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

Continued on next page...

1Only 5 zip-ties required for assembly.

Appendix A. Commercial Off-The-Shelf Parts Information | 17
Item | Part Number | Vendor | QTY | Cost / Item | Ext. Cost | Curr.
Continuous Flex Wire, 26 AWG | McMaster-Carr 7071K19 (https://www.mcmaster.com/7071K19/) | McMaster-Carr | 50 feet | $1.20 | $60.00 | USD
M2 x 25 mm Cheese Head Slotted Machine Screw | McMaster-Carr 91800A023 (https://www.mcmaster.com/91800A023/) | McMaster-Carr | Pack of 50*² | $8.41 | $8.41 | USD
M2 18-8 Washer | McMaster-Carr 93475A195 (https://www.mcmaster.com/93475A195/) | McMaster-Carr | Pack of 100³ | $1.06 | $1.06 | USD
APPROXIMATE TOTAL: | | | | | $550⁴ | CAD

End of table.

2Only 23 screws needed for assembly.
3Only 16 washers needed for assembly.
4This is a rough estimate, assuming $1.35 CAD = $1.00 USD. Delivery fees and taxes are not included.

18

# B Grip Pattern Template

The following page contains a template you can use to cut out the neoprene rubber grips. When printing this page, be sure to check in your print settings that you are using the original scale of the document.

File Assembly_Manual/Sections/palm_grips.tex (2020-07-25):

% Palm Grips

\chapter{Palm Grips}  % Main chapter title

\label{Palm Grips} 
%---------------------------------------------------------------------------------------------------------------------------------------
%
% PALM GRIPS	
%
%---------------------------------------------------------------------------------------------------------------------------------------

\textit{Estimated time 1h 15m}

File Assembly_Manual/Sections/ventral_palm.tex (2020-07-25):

% Ventral Palm Cover and USB Webcam

\chapter{Ventral Palm Cover and USB Webcam}  % Main chapter title

\label{Ventral Palm Cover and USB Webcam} 
%---------------------------------------------------------------------------------------------------------------------------------------
%
% Ventral Palm Cover and USB Webcam
%
%---------------------------------------------------------------------------------------------------------------------------------------

\textit{Estimated time 0h 20m}

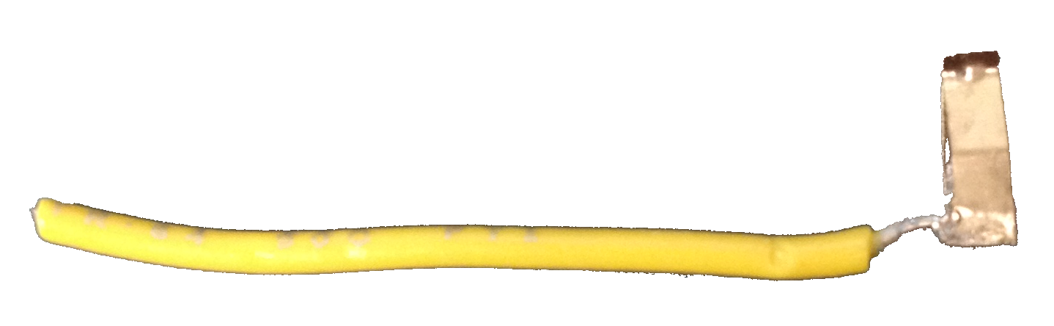
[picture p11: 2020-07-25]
Assembly_Manual/Figures/Wire soldered to clip.png

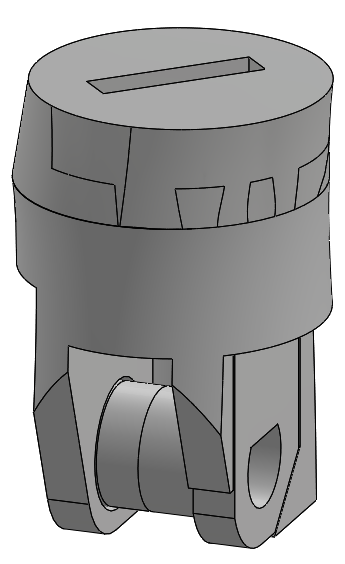
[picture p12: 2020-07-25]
Assembly_Manual/Figures/Twist Lock 2.PNG

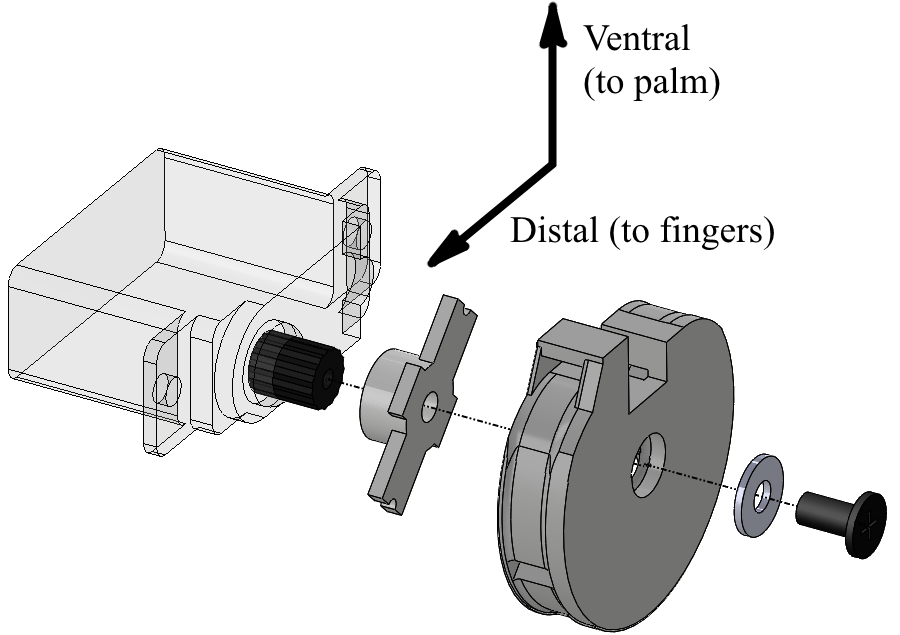
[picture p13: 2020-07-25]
Assembly_Manual/Figures/Servo Spool Installation.PNG

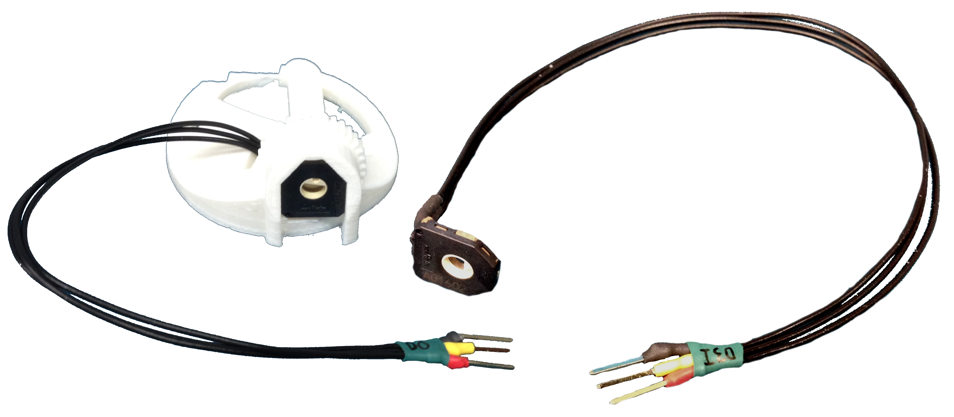
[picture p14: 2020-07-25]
Assembly_Manual/Figures/Finished Pots.png

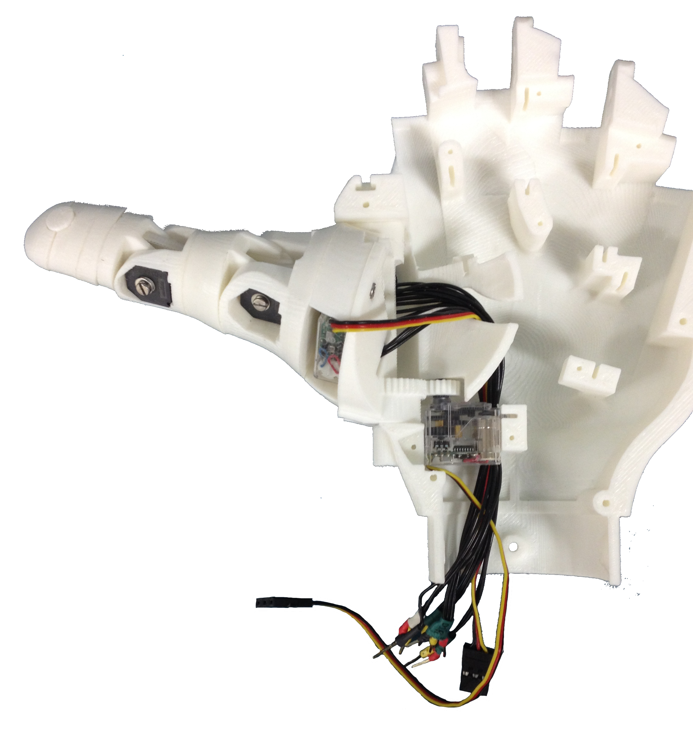
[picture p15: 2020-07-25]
Assembly_Manual/Figures/Thumb Mounted.png

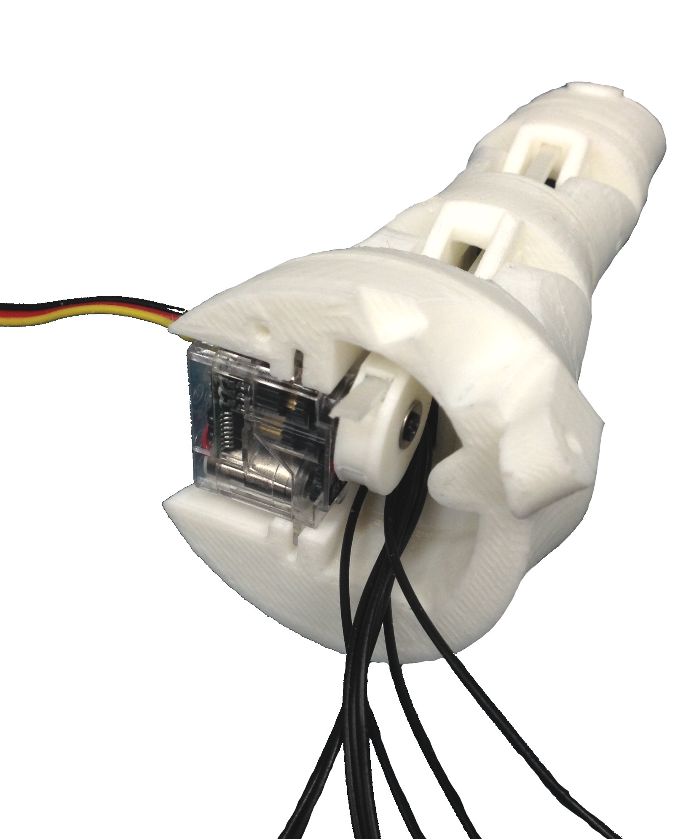
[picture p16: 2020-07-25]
Assembly_Manual/Figures/Thumb Servo Installed.jpg

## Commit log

2020-05-01 Adds MUX_Assembly.STEP
    [MUX_Assembly.STEP]
2020-05-01 Adds Fit Test.STEP
    Fit Test is an assembly of all relevant parts to test the fit of the MUX board in the wrist.
2020-07-24 Create Assembly_Manual.md
    Quick conversion of previous manual using markdown converter
2020-07-24 Adds Assembly Manual pdf
2020-07-25 Adds Initial LaTeX assembly manual and figures
    [Pot to Servo Control 6.fzz, Pot to Servo Control.fzz]
2020-07-25 Adds sections to assembly manual
2020-07-27 Adds sensor/electronics BOM
2020-11-11 Updates to assembly manual
